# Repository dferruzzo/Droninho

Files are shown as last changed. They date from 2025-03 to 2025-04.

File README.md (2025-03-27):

# Droninho

Este repositório apresenta um diagrama eletrônico esquemático feito em [KiCad 9.0](https://www.kicad.org/) de um drone pequeno baseado em ESP32. 

---

## Objetivo

- Produzir a placa de circuito impresso do hardware do droninho.

---

## To-Do

- [x] ERC OKAY!
- [x] Criar PCB.
- [x] Checar footprint do conectores *J2, J3, J4, J5*.
- [x] Checar footprint do conector da bateria *J1*.
- [x] Checar PCB rules. Corrigir footprint do MPU9250.
- [x] Add connector for I2C and Power to connect other components for testing
- [x] Consider connection for RC receiver (cancelled!).
- [x] O MPU9250 está muito perto do ESP32 na placa.
- [x] Adicionar layer com nomes dos componentes e conectores. 
- [x] For review.
- [x] Duvida: A distancia entre a entrada USB do ESP32 e o MPU9250 é suficiente? Não.
- [x] Mudar de lado o ESP32 OK.
- [x] Mudar footprint dos diodos e resistências OK.
- [x] Colocar uma fonte regulada de 3.3v. https://docs.espressif.com/projects/esp-dev-kits/en/latest/esp32/esp32-devkitc/user_guide.html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 https://dl.espressif.com/dl/schematics/esp32_devkitc_v4_sch.pdf
- [x] Mudar os footprints dos conectores dos motores e da bateria (só da bateria).
- [ ] Mandar a produzir com PCBway.

---
 
## Esquemático

[Diagrama elétrico esquemático.](schematics.pdf)

---

## PCB

PCB Front

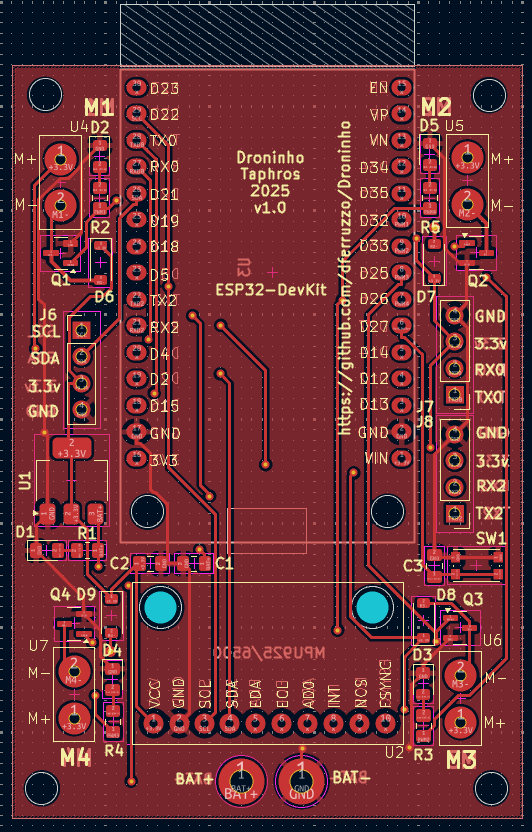
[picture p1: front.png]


PCB Back

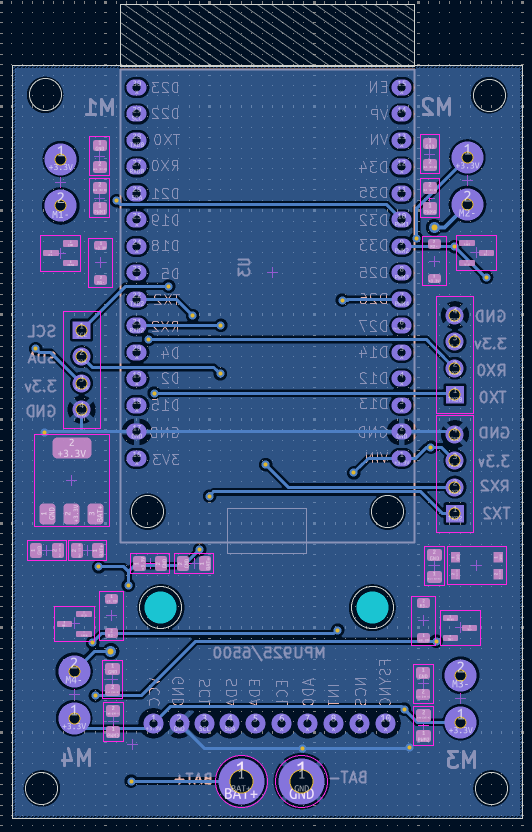
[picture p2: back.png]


---

## 3D model

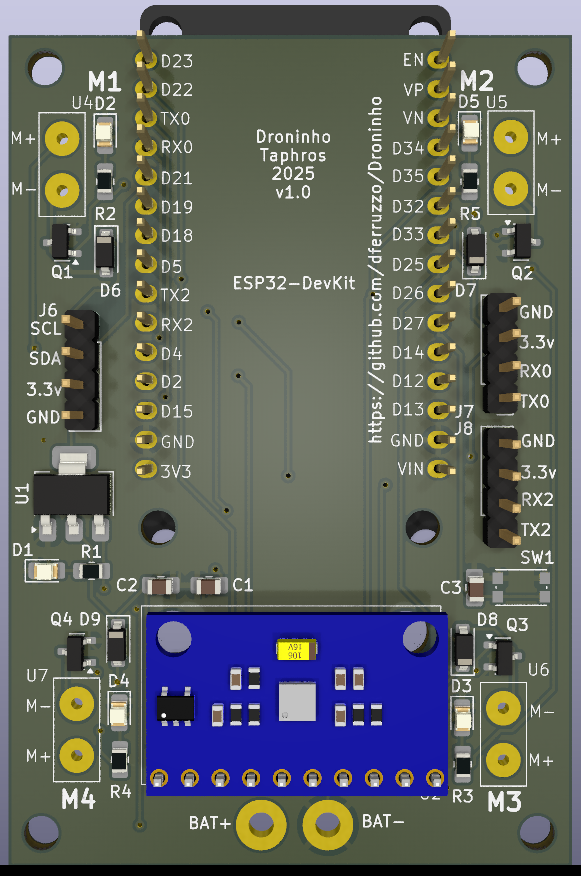
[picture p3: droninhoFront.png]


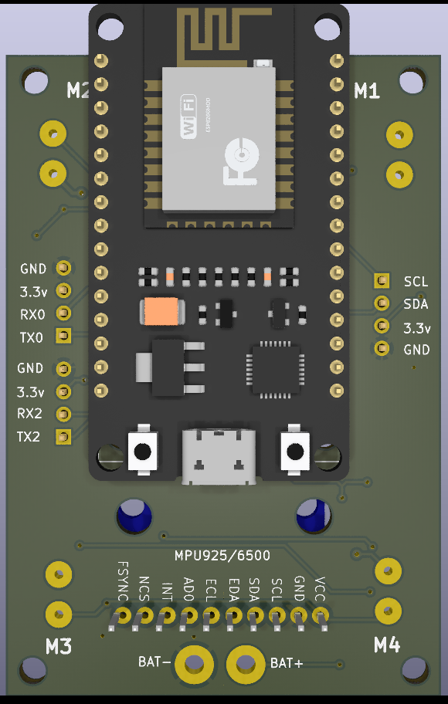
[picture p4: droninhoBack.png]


---

## Como Contribuir

1. Faça um fork deste repositório.
2. Crie uma branch para sua feature (`git checkout -b feature/nome-da-feature`).
3. Faça commit das suas alterações (`git commit -m 'Adiciona nova feature'`).
4. Faça push para a branch (`git push origin feature/nome-da-feature`).
5. Abra um Pull Request.

---

## Licença

Este projeto está licenciado sob a licença MIT.

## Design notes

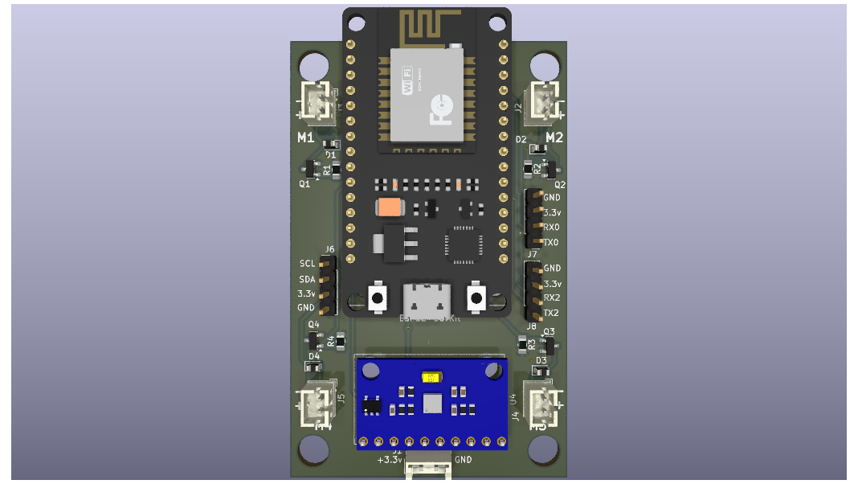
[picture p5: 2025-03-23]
droninho.png

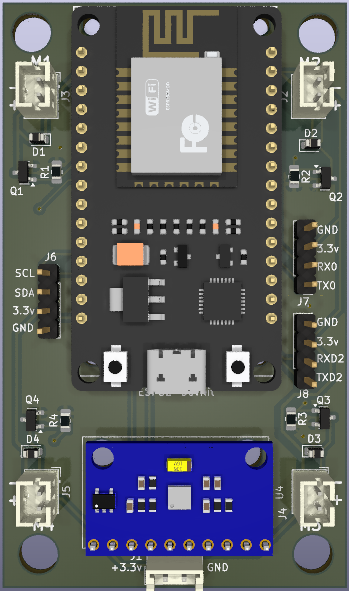
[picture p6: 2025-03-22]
3Dmodel.png

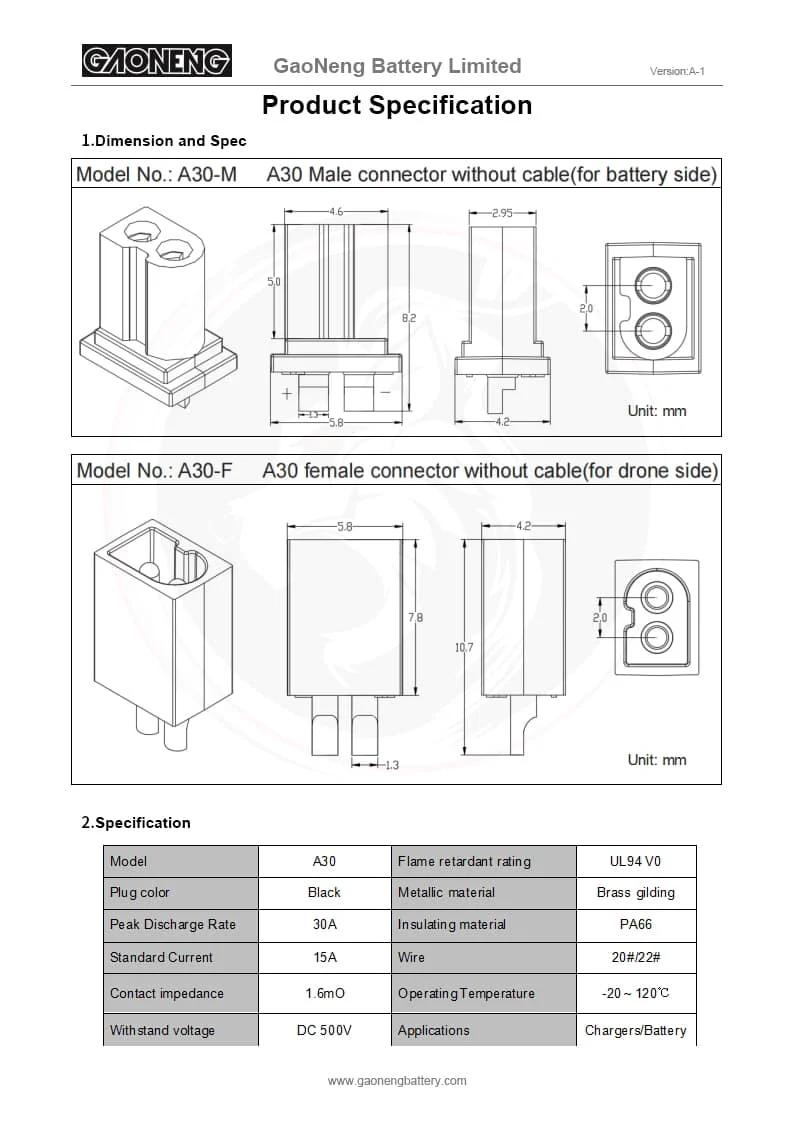
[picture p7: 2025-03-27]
Documentation/Conector-A30.png

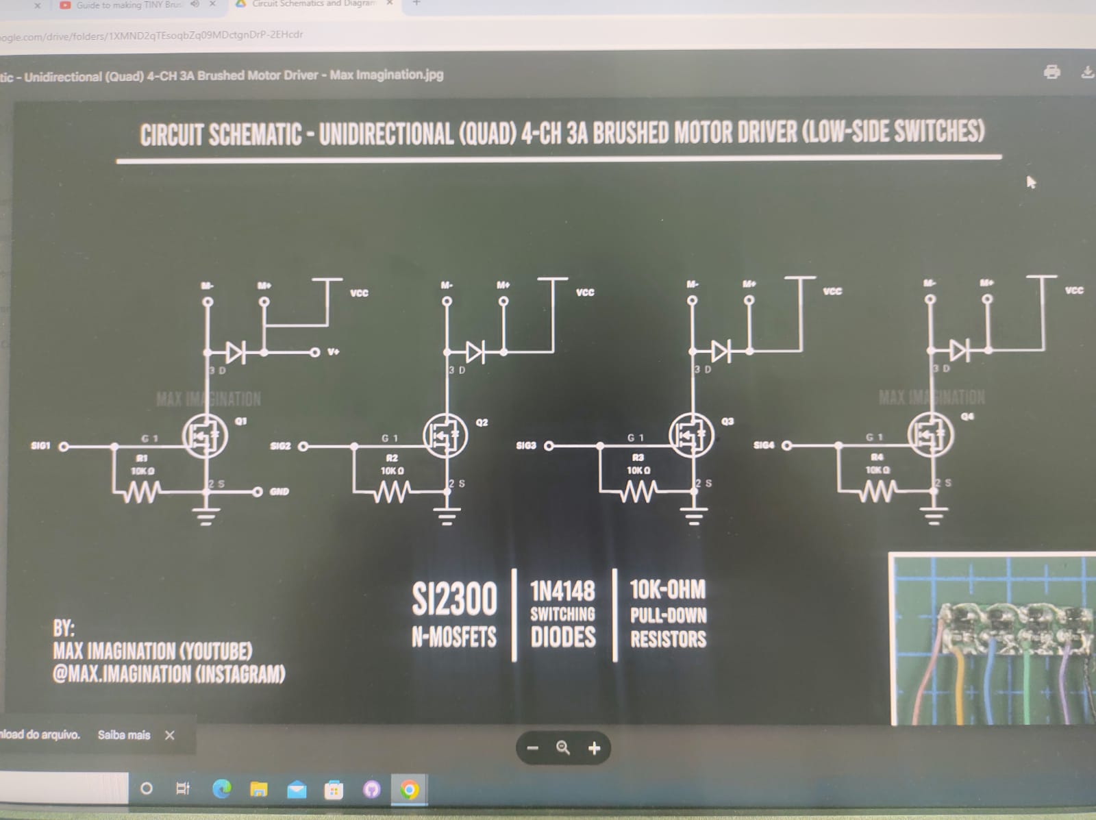
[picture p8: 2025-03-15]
Documentation/etapa_potencia.jpeg

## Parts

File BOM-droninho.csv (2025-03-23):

Id | Designador | Footprint | Quantidade | Designação | Fornecedor e referência
1 | R2,R1,R4,R3 | R_0805_2012Metric_Pad1.20x1.40mm_HandSolder | 4 | 10K
2 | Q1,Q4,Q2,Q3 | SOT-23 | 4 | SI2300
3 | J5 | JST_PH_B2B-PH-K_1x02_P2.00mm_Vertical | 1 | M4
4 | J7 | PinHeader_1x04_P2.54mm_Vertical | 1 | TXD0/RXD0
5 | J8,J6 | PinHeader_1x04_P2.54mm_Vertical | 2 | I2C
6 | J2 | JST_PH_B2B-PH-K_1x02_P2.00mm_Vertical | 1 | M2
7 | D4,D3,D2,D1 | D_SOD-110 | 4 | 1N4148
8 | J3 | JST_PH_B2B-PH-K_1x02_P2.00mm_Vertical | 1 | M1
9 | U1 | ESP32_30pin vertical WIFI | 1 | ESP32 Dev Kit
10 | J4 | JST_PH_B2B-PH-K_1x02_P2.00mm_Vertical | 1 | M3
11 | U4 | MPU-9250-6500 | 1 | MPU9250/6500
12 | J1 | JST_EH_B2B-EH-A_1x02_P2.50mm_Vertical | 1 | Conn_01x02_Pin

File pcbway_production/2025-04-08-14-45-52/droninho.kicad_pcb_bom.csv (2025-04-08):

Designator | Quantity | Value | Footprint | Package | MPN | DNP | Mount_Type | Description | Manufacturer | Mfg Part # | Package/Footprint | Type | Sim.Pins | Sim.Device
[C1]C1; [C2]C2 | 2 | 22uF/10V(20%) | C_0805_2012Metric_Pad1.18x1.45mm_HandSolder | C_0805_2012Metric_Pad1.18x1.45mm_HandSolder |  |  | smt | Unpolarized capacitor, small symbol | Murata Electronics | GRM21BR61A226ME51L | 0805 | SMD
C3 | 1 | 0.1uF/10V(5%) | C_0805_2012Metric_Pad1.18x1.45mm_HandSolder | C_0805_2012Metric_Pad1.18x1.45mm_HandSolder |  |  | smt | Unpolarized capacitor, small symbol | Murata Electronics | GRM21B7U1A104JA01L | 0805 | SMD
D1 | 1 | RED LED | LED_0805_2012Metric_Pad1.15x1.40mm_HandSolder | LED_0805_2012Metric_Pad1.15x1.40mm_HandSolder |  |  | smt | Light emitting diode | Wurth Elektronik | 150080RS75000 | 0805 | SMD | 1=K 2=A
[D2]D2; [D3]D3; [D4]D4; [D5]D5 | 4 | WHITE LED | LED_0805_2012Metric_Pad1.15x1.40mm_HandSolder | LED_0805_2012Metric_Pad1.15x1.40mm_HandSolder |  |  | smt | Light emitting diode | Broadcom / Avago | [D2]HSMW-C170 ; [D3,D4,D5]HSMW-C170 | 0805 | SMD | 1=K 2=A
[D6]D6; [D7]D7; [D8]D8; [D9]D9 | 4 | 1N4148W SOD-123 SMD 100V 2A (A2) | D_SOD-123 | D_SOD-123 |  |  | smt | 100V 0.15A standard switching diode, DO-35 | Diotec Semiconductor | 1N4148W | SOD-123F | SMD | 1=K 2=A | D
[J6]J6; [J8]J8 | 2 | I2C | PinHeader_1x04_P2.54mm_Vertical | PinHeader_1x04_P2.54mm_Vertical |  |  | tht | Generic connector, single row, 01x04, script generated | Molex | 502603-0470 | 4POS | THT
J7 | 1 | TXD0/RXD0 | PinHeader_1x04_P2.54mm_Vertical | PinHeader_1x04_P2.54mm_Vertical |  |  | tht | Generic connector, single row, 01x04, script generated | Molex | 502603-0470 | 4POS | THT
[Q1]Q1; [Q2]Q2; [Q3]Q3; [Q4]Q4 | 4 | Si2300DS | SOT-23 | SOT-23 |  |  | smt | N-MOSFET transistor, gate/source/drain | Vishay | SI2300DS-T1-BE3 | SOT-23 (TO-236) | SMD
[R1]R1; [R2]R2; [R3]R3; [R4]R4; [R5]R5 | 5 | 10K(1%) | R_0805_2012Metric_Pad1.20x1.40mm_HandSolder | R_0805_2012Metric_Pad1.20x1.40mm_HandSolder |  |  | smt | Resistor, US symbol | Panasonic | ERJ-6ENF1002V | 0805 | SMD
SW1 | 1 | KMR241G LFS | SW_Push_1P1T_NO_CK_KMR2 | SW_Push_1P1T_NO_CK_KMR2 |  |  | smt | Push button switch, generic, two pins | C&K | KMR241G LFS | SW_Push_1P1T_NO_CK_KMR2 | SMT
U1 | 1 | AMS1117-3.3 | SOT-223-3_TabPin2 | SOT-223-3_TabPin2 |  |  | smt | 1A Low Dropout regulator, positive, 3.3V fixed output, SOT-223
U2 | 1 | MPU9250/6500 | MPU-9250-6500 | Not applicable |  |  | tht | MPU9250/6500 board
U3 | 1 | ESP32 ESP-WROOM-32 DEVKit V1 | ESP32_30pin vertical WIFI | Not applicable |  |  | tht | ESP32 DEVKIT board
U4, U5, U6, U7 | 4 | Through Hole Connector | Connector_Motor | Not applicable |  |  | tht | Motor connector

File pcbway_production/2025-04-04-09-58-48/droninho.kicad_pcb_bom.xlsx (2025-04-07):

 |  |  | xxxx xxxx xxxxx xxPCS BOM (Sample Bill of Materials)
Item # | *Designator | *Qty | Manufacturer | *Mfg Part # | Description / Value | *Package/Footprint | Type | Your Instructions / Notes
1 | U1 | 1 | Linear | LTC3780EG#PBF | IC BUCK-BOOST CONV 24-SSOP | 24-SSOP | SMD
2 | U2,U4 | 2 | Fairchild | LM2904M | IC OPAMP DUAL -40-85 C 8-SOIC | 8-SOIC | DNS
3 | U3 | 1 | ON | LM317MBDTG | LM317M IC REG VOLT ADJ 500MA DPAK | DPAK | SMD
4 | U5 | 1 | Microchip | PIC16F690-I/SS | IC PIC MCU FLASH 4KX14 20SSOP | 20SSOP | SMD
5 | Q1 | 1 | Diodes Inc | GBJ10005-F | RECT BRIDGE GPP 50V 10A GBJ | GBJ | SMD
6 | R14,R18 | 2 | Panasonic | ERJ-6ENF4701V | RES 4.70K OHM 1/8W 1% 0805 SMD | 0805 | SMD
7 | R15 | 1 | Susumu | RL3720WT-R022-F | RES .022 OHM 1W 1% 0815 SMD | 0815 | SMD
8 | R16, R31 | 2 | Panasonic | ERJ-6ENF4702V | RES 47.0K OHM 1/8W 1% 0805 SMD | 0805 | SMD
9 | C5 | 1 | Murata | GRM21BR71C225KA12L | CAP CER 2.2UF 16V X7R 0805 | 0805 | SMD
10 | C7 | 1 | Murata | GRM21BR71C475KA73L | CAP CER 4.7UF 16V X7R 0805 | 0805 | DNS
11 | C8,C22 | 2 | Muruta | GRM21BR71C105KA01L | CAP CER 1.0UF 16V 10% X7R 0805 | 0805 | SMD
12 | CN6 | 1 | Molex | 538-53398-0671 | 1.25mm Connectors VERTICAL HDR SMT 6P | SMT 6P | SMD
13 | L1,L2 | 2 | Coiltronics | DR127-150-R | INDUCTOR SHIELD PWR 15UH SMD | SMD | SMD
14 | L3 | 1 | TDK | ACM1211-102-2PL-TL | CHOKE COMM MODE 1000 OHM 6A SM | SMD | SMD
15 | CN3,CN4 | 2 | Molex | 53047-0510 | CONN HEADER 5POS 1.25MM VERT TIN | 5POS | thru-hole
Need a quick and accurante quote? Need an efficient production? Please read SMT Ordering Necessary Files & Info in 1 minute. Thank you very much! (https://www.pcbway.com/smt_ordering_guide.html)
Click for Instructions on How to Create a BOM (https://www.pcbway.com/blog/PCB_Assembly/How_to_Build_a_BOM__Bill_Of_Materials_.html)

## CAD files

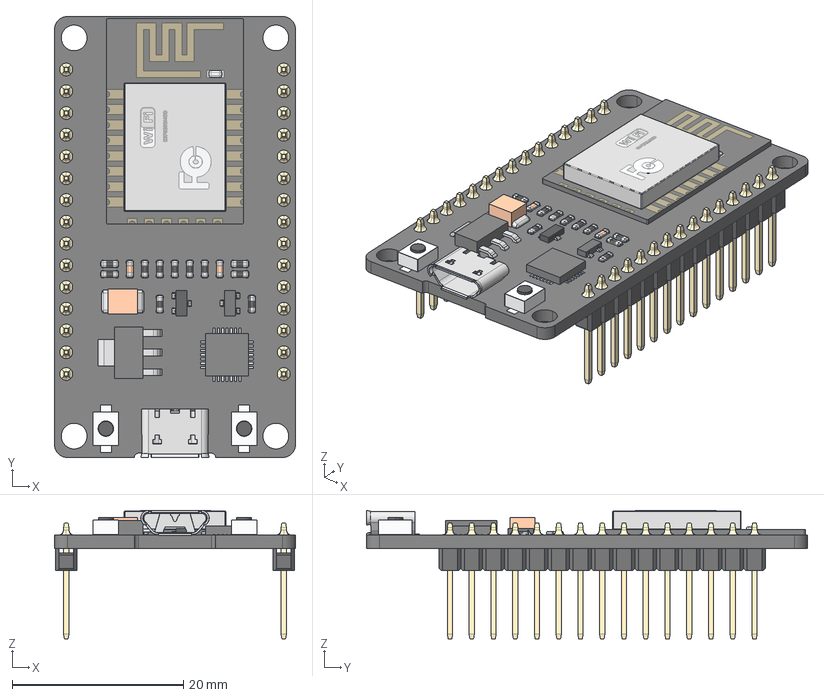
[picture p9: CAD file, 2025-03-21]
3Dmodels/esp32_dev_kit_v1_asm.stp
28.1 x 51.5 x 15.0 mm
PCB
PIN x 30
WIFI_CARD_2
RECTANGULARCHIP_2
MICROCHIP_2
TANCHIP_2
TRANSISTOR_3-LEG_2
RESISTOR1_2 x 11
RESISTOR2-32_2 x 2
TRANSISTOR_3-LEG2_2
BUTTONFLASH-13_2 x 2
BUTTONFLASH-14_2 x 2
USB_SOCKET_2

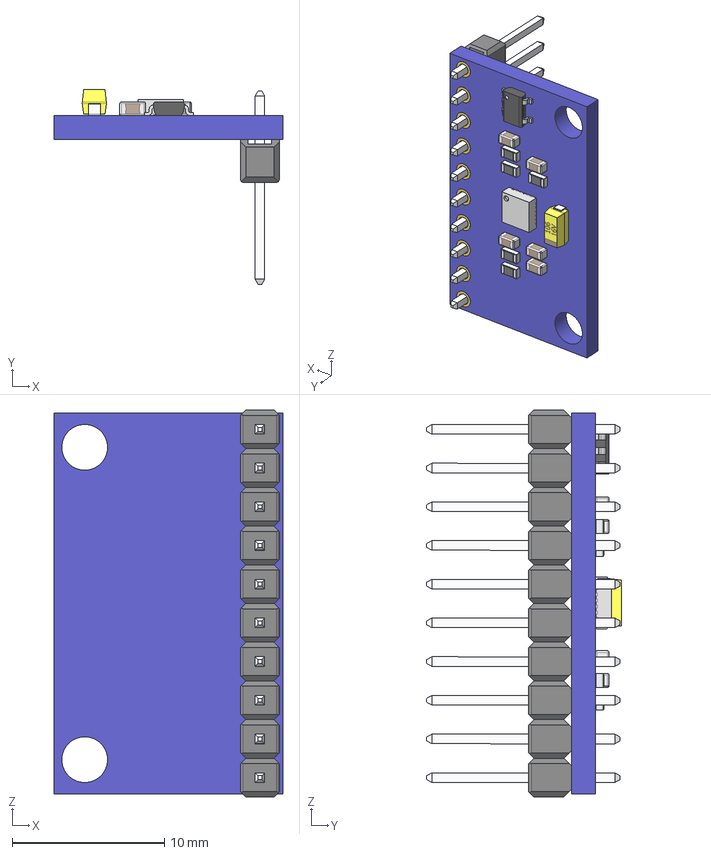
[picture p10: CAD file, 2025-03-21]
3Dmodels/MPU-9250.stp
15.0 x 12.8 x 25.4 mm
board
hole_plating x 20
Pin Header 1x10 TH Pitch 2.54mm
MPU-9250_1
tantalum 10uF
SOT23_5
RESC-0603 x 5
CAPC-0603-T0.9-BN x 5

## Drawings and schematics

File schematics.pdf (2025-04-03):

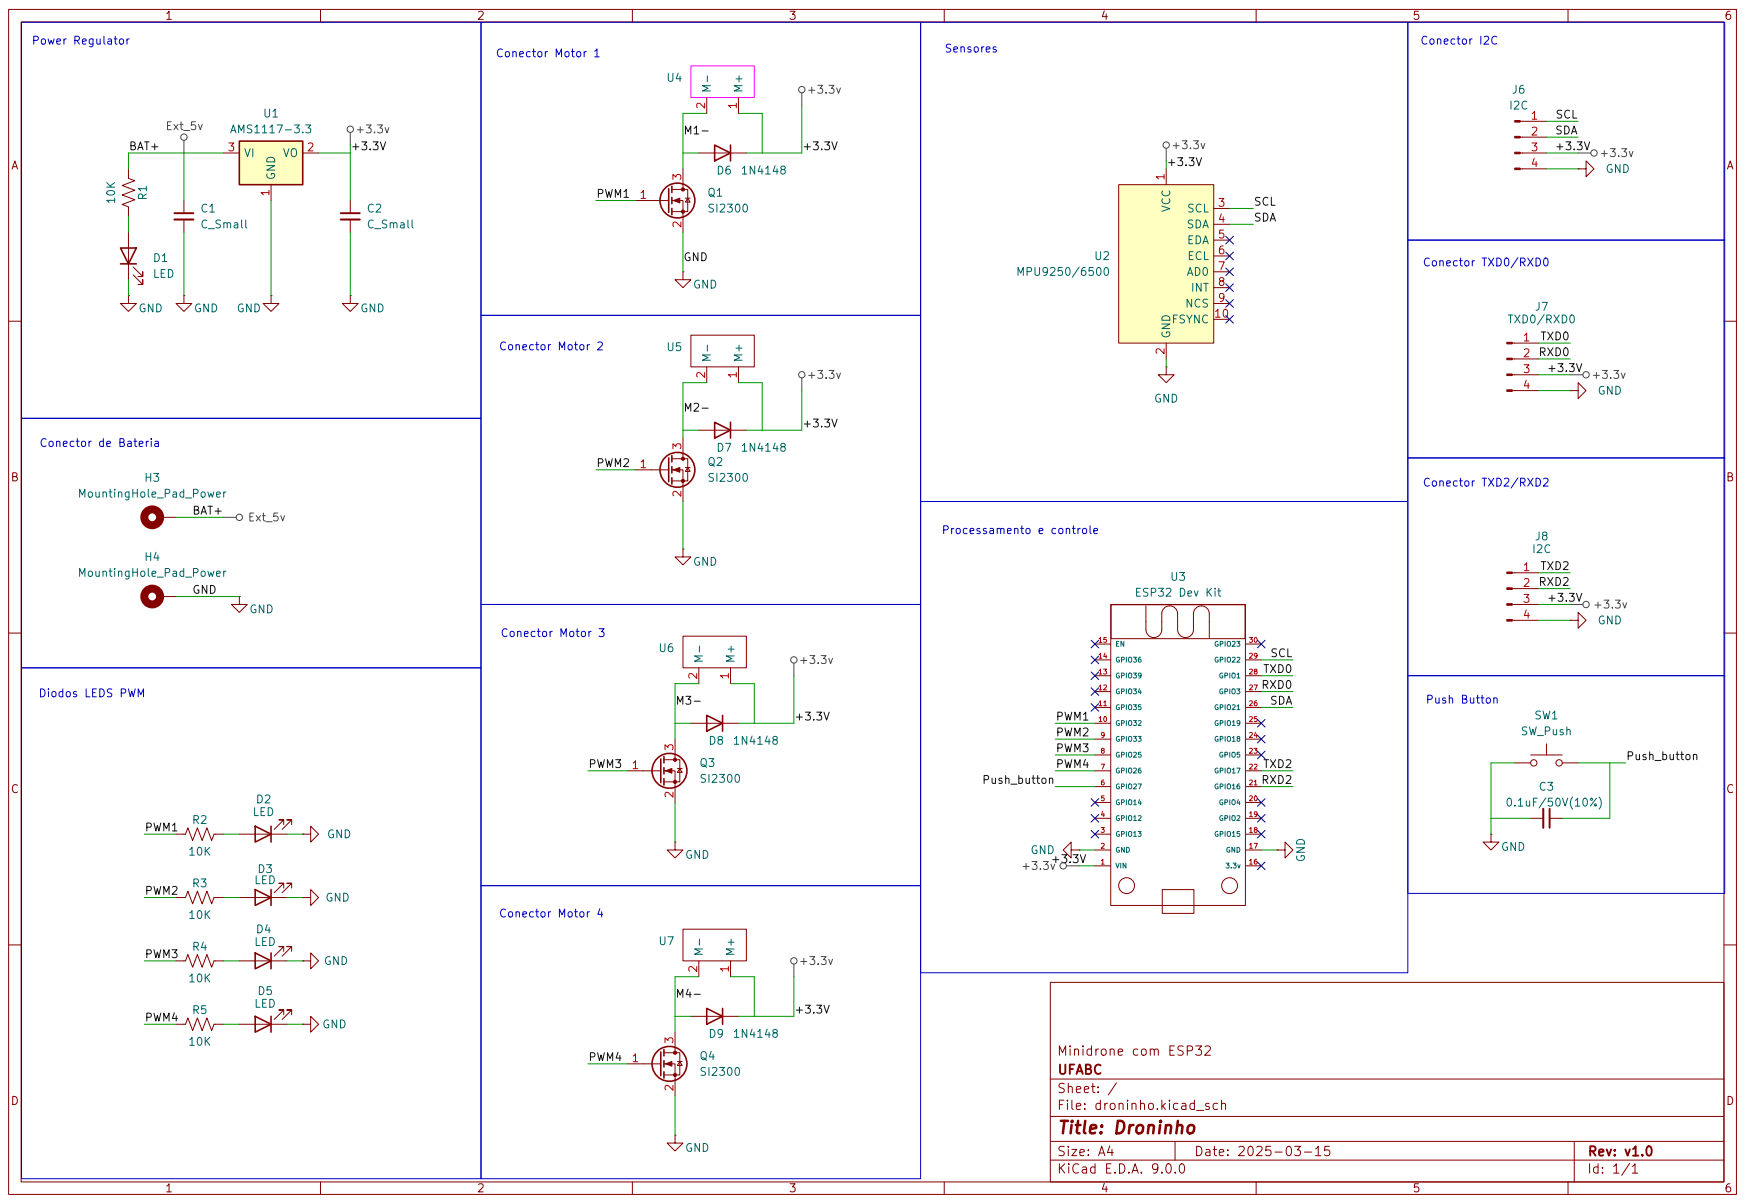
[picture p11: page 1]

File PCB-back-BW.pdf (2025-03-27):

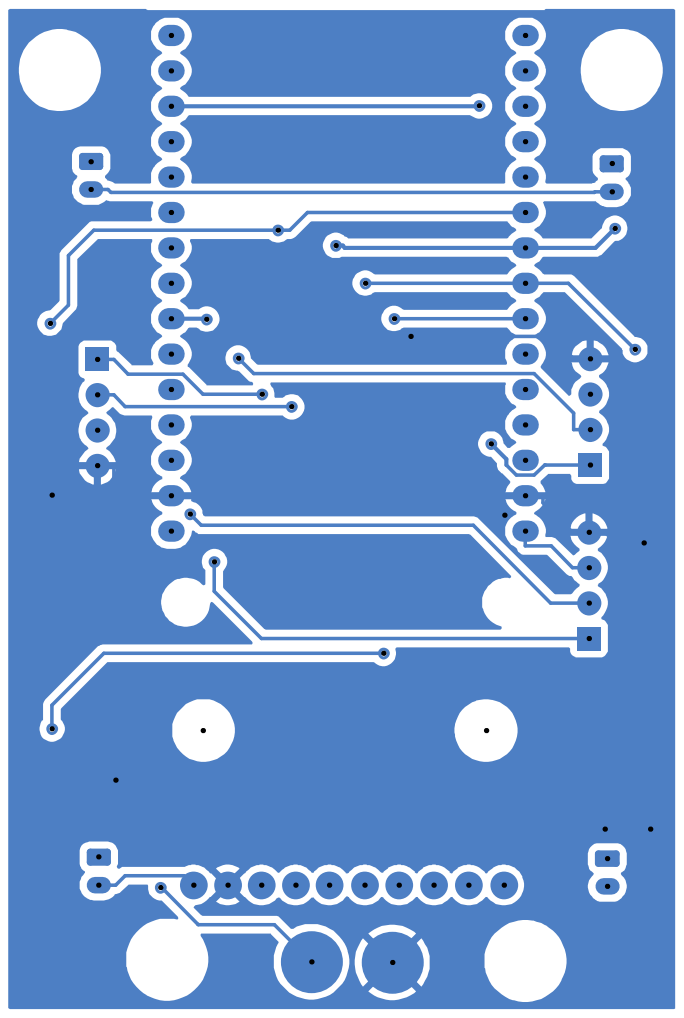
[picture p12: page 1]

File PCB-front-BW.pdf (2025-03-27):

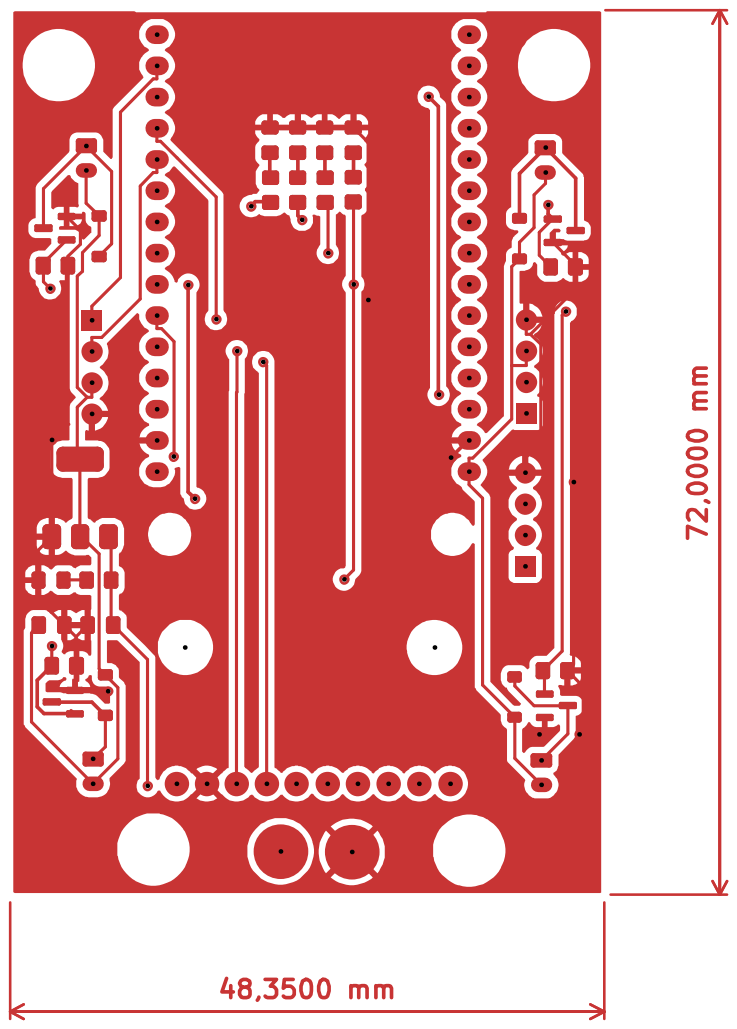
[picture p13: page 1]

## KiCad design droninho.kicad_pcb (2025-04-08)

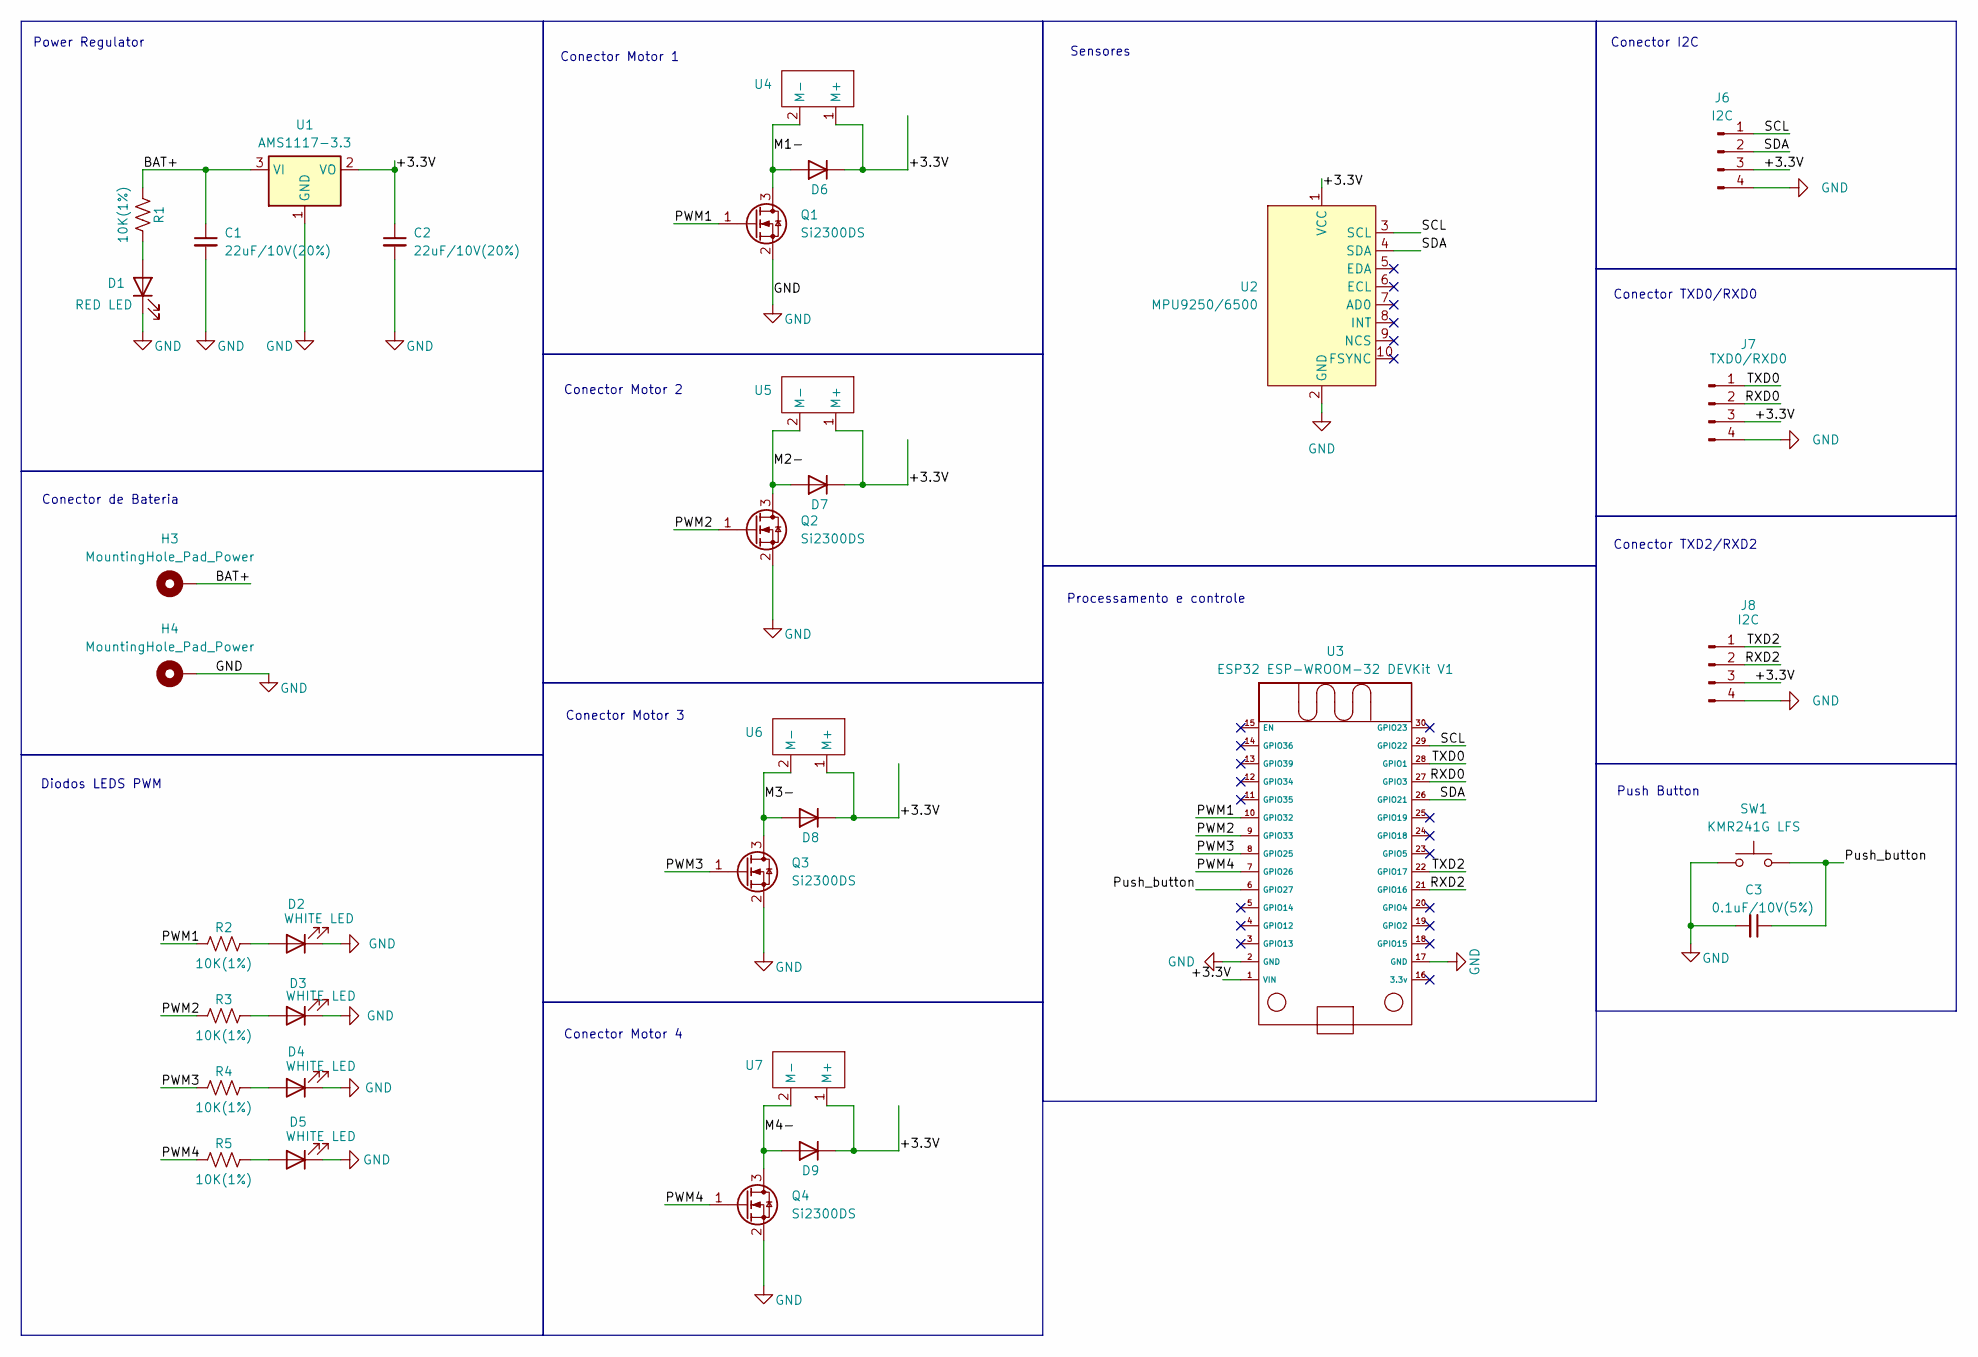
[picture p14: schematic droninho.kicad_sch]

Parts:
C1, C2: 22uF/10V(20%); C_0805_2012Metric_Pad1.18x1.45mm_HandSolder; Mfg Part # GRM21BR61A226ME51L
C3: 0.1uF/10V(5%); C_0805_2012Metric_Pad1.18x1.45mm_HandSolder; Mfg Part # GRM21B7U1A104JA01L
D1: RED LED; LED_0805_2012Metric_Pad1.15x1.40mm_HandSolder; Mfg Part # 150080RS75000
D2, D3, D4, D5: WHITE LED; LED_0805_2012Metric_Pad1.15x1.40mm_HandSolder; Mfg Part # HSMW-C170
D6, D7, D8, D9: 1N4148W SOD-123 SMD 100V 2A (A2); D_SOD-123; Mfg Part # 1N4148W
H3, H4: MountingHole_Pad_Power; MountingHole_2.2mm_M2_Pad_TopBottom
J6, J8: I2C; PinHeader_1x04_P2.54mm_Vertical; Mfg Part # 502603-0470
J7: TXD0/RXD0; PinHeader_1x04_P2.54mm_Vertical; Mfg Part # 502603-0470
Q1, Q2, Q3, Q4: Si2300DS; SOT-23; Mfg Part # SI2300DS-T1-BE3
R1, R2, R3, R4, R5: 10K(1%); R_0805_2012Metric_Pad1.20x1.40mm_HandSolder; Mfg Part # ERJ-6ENF1002V
SW1: KMR241G LFS; SW_Push_1P1T_NO_CK_KMR2; Mfg Part # KMR241G LFS
U1: AMS1117-3.3; SOT-223-3_TabPin2
U2: MPU9250/6500; MPU-9250-6500
U3: ESP32 ESP-WROOM-32 DEVKit V1; ESP32_30pin vertical WIFI
U4, U5, U6, U7: Through Hole Connector; Connector_Motor

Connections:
/+3.3V: C2.1, D6.1 (K), D7.1 (K), D8.1 (K), D9.1 (K), J6.3, J7.3, J8.3, U1.2 (VO), U2.1 (VCC), U3.1 (VIN), U4.1 (M+), U5.1 (M+), U6.1 (M+), U7.1 (M+)
/BAT+: C1.1, H3.1, R1.1, U1.3 (VI)
/M1-: D6.2 (A), Q1.3 (D), U4.2 (M-)
/M2-: D7.2 (A), Q2.3 (D), U5.2 (M-)
/M3-: D8.2 (A), Q3.3 (D), U6.2 (M-)
/M4-: D9.2 (A), Q4.3 (D), U7.2 (M-)
/PWM1: Q1.1 (G), R2.1, U3.10 (GPIO32)
/PWM2: Q2.1 (G), R3.1, U3.9 (GPIO33)
/PWM3: Q3.1 (G), R4.1, U3.8 (GPIO25)
/PWM4: Q4.1 (G), R5.1, U3.7 (GPIO26)
/Push_button: C3.1, SW1.2, U3.6 (GPIO27)
/RXD0: J7.2, U3.27 (GPIO3)
/RXD2: J8.2, U3.21 (GPIO16)
/SCL: J6.1, U2.3 (SCL), U3.29 (GPIO22)
/SDA: J6.2, U2.4 (SDA), U3.26 (GPIO21)
/TXD0: J7.1, U3.28 (GPIO1)
/TXD2: J8.1, U3.22 (GPIO17)
GND: C1.2, C2.2, C3.2, D1.1 (K), D2.1 (K), D3.1 (K), D4.1 (K), D5.1 (K), H4.1, J6.4, J7.4, J8.4, Q1.2 (S), Q2.2 (S), Q3.2 (S), Q4.2 (S), SW1.1, U1.1 (GND), U2.2 (GND), U3.2 (GND), U3.17 (GND)
unnamed: D1.2 (A), R1.2
unnamed: D2.2 (A), R2.2
unnamed: D3.2 (A), R3.2
unnamed: D4.2 (A), R4.2
unnamed: D5.2 (A), R5.2

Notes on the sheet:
Conector TXD0/RXD0
Conector Motor 3
Conector Motor 4
Diodos LEDS PWM
Conector de Bateria
Conector Motor 2
Conector I2C
Sensores
Processamento e controle
Conector Motor 1
Power Regulator
Push Button
Conector TXD2/RXD2

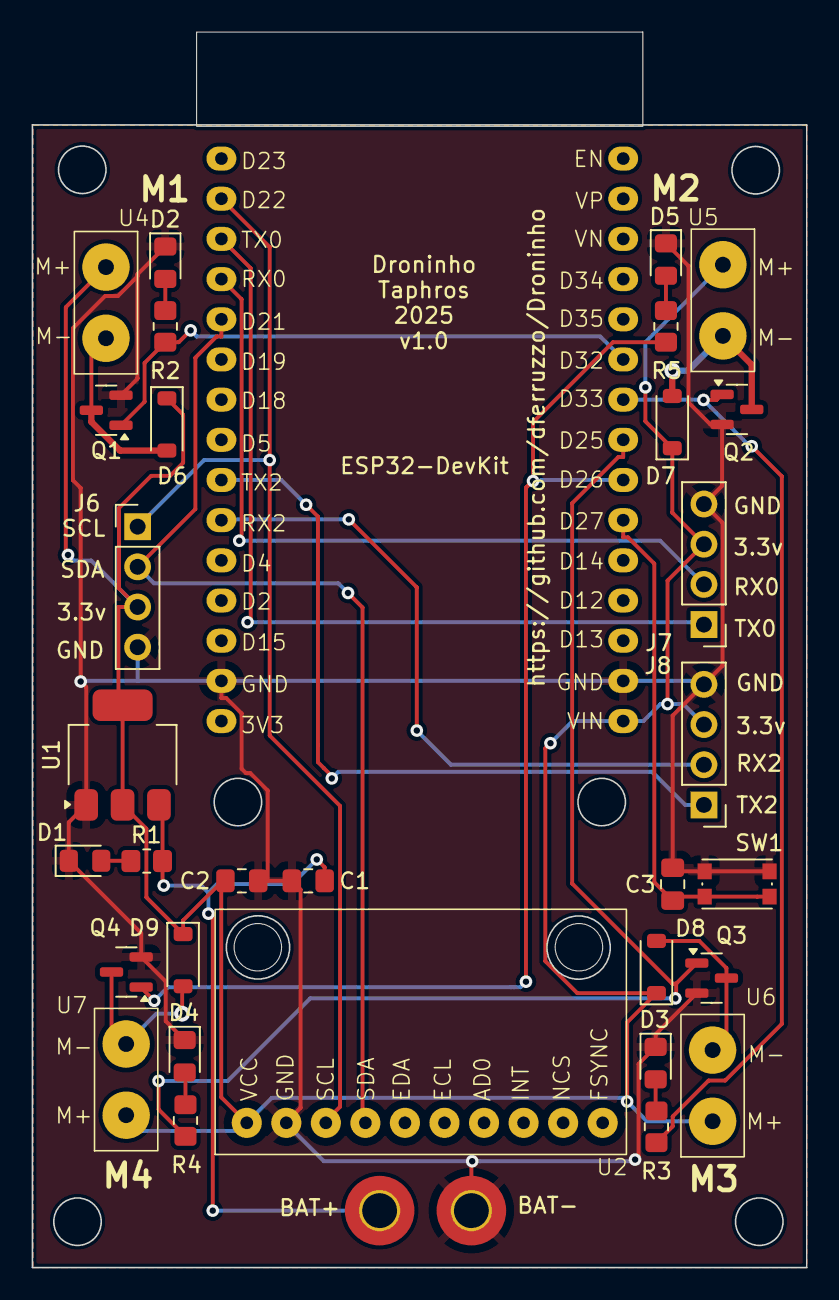
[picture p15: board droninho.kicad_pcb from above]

Board: 2 copper layers, 49.0 x 78.1 mm, 34 parts (1 on the bottom side), 23 nets.

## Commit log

2025-03-16 Electrical part finished
    [droninho.kicad_pcb, droninho.kicad_sch]
2025-03-16 Readme added
    [droninho.kicad_pcb, droninho.kicad_sch]
2025-03-16 add nets to schematic
    [droninho.kicad_pcb, droninho.kicad_sch]
2025-03-16 ERC OK!
    [droninho.kicad_pcb, droninho.kicad_sch]
2025-03-18 ERC Done
    [droninho.kicad_pcb, droninho.kicad_sch]
2025-03-19 PCB feito.
    [droninho.kicad_pcb]
2025-03-19 Footprints checked.
    [droninho.kicad_pcb, droninho.kicad_sch]
2025-03-21 PCB finalizado.
    [MPU-9250.stp, droninho.kicad_pcb, droninho.kicad_sch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]
2025-03-22 Ready for review.
    [droninho.kicad_pcb, droninho.kicad_sch]
2025-03-22 small changes
    [droninho.kicad_pcb]
2025-03-22 PDF PCB-front and PCB-back added.
2025-03-23 Versão com WIFI de fora da placa.
    [droninho.kicad_pcb, droninho.kicad_sch]
2025-03-23 BOM, DCR e erc OKAY.
    [BOM-droninho.csv, droninho.kicad_pcb, droninho.kicad_pcb_bom.csv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]
2025-03-25 Correções em footprints e troca de lado do ESP32.
    [droninho.kicad_pcb, droninho.kicad_sch]
2025-03-26 voltage regulator added
    [droninho.kicad_sch]
2025-03-27 ERC done!
    [droninho.kicad_sch]
2025-03-27 Source and Battery connector added!
    [droninho.kicad_pcb, droninho.kicad_sch]
2025-04-03 pull-down resistors removed, change leds positions.
    [droninho.kicad_pcb, droninho.kicad_pcb_bom.csv, droninho.kicad_pcb_positions.csv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]
2025-04-03 Ajustes finais no PCB
    [droninho.kicad_pcb]
2025-04-04 packages updated
    [droninho.kicad_pcb_bom.csv, droninho.kicad_pcb_positions.csv, droninho.kicad_sch]
2025-04-04 Cleaning up.
    [droninho.kicad_pcb_bom.csv, droninho.kicad_pcb_positions.csv]
2025-04-07 add manufacturer and part number for BOM.
    [droninho.kicad_pcb, droninho.kicad_pcb_bom.csv, droninho.kicad_pcb_bom.xlsx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]
2025-04-08 BOM updated.
    [droninho.kicad_pcb, droninho.kicad_pcb_bom.csv, droninho.kicad_pcb_positions.csv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]
